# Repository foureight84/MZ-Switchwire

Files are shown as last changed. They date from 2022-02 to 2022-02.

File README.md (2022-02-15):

## Anycubic Mega Zero v1 Switchwire Mod

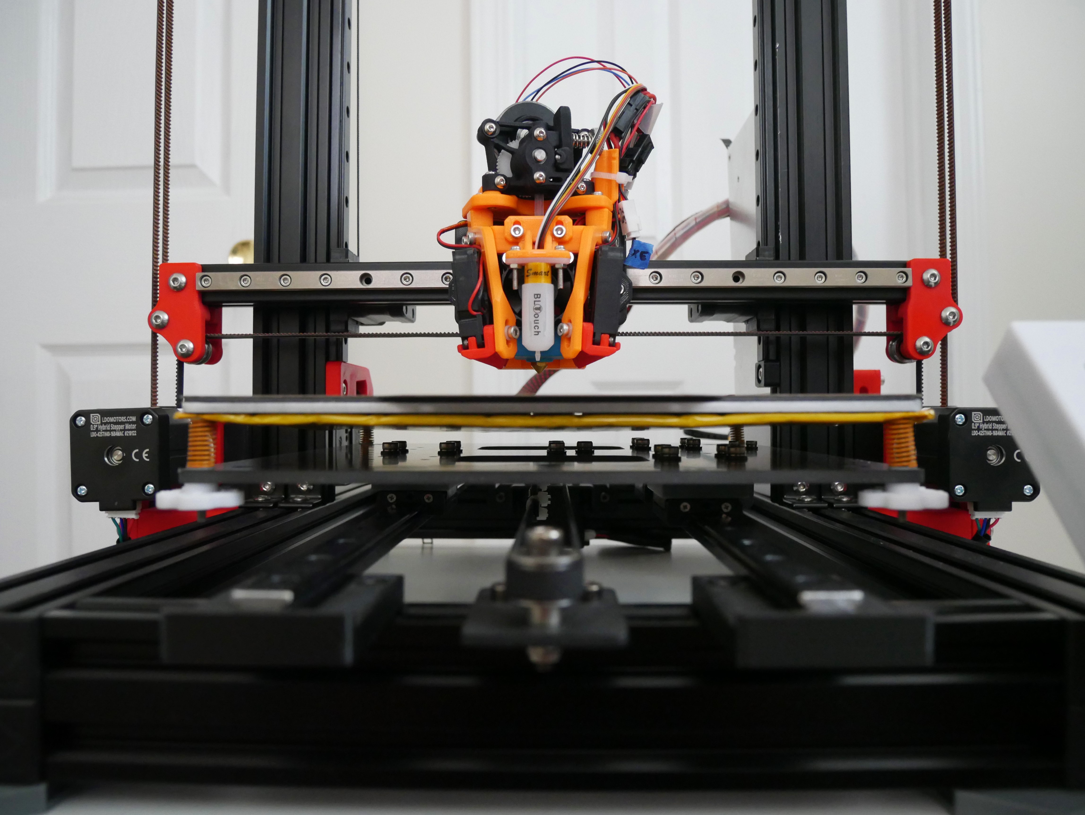
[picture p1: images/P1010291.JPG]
MZ Switchwire


### [390mm X-Axis with MGN9H](https://foureight84.github.io/Anycubic-Mega-Zero-1.0%20-%20Switchwire%20MGN9H%20Gantry-sfa.html "View STEP file") - Click for 3D preview
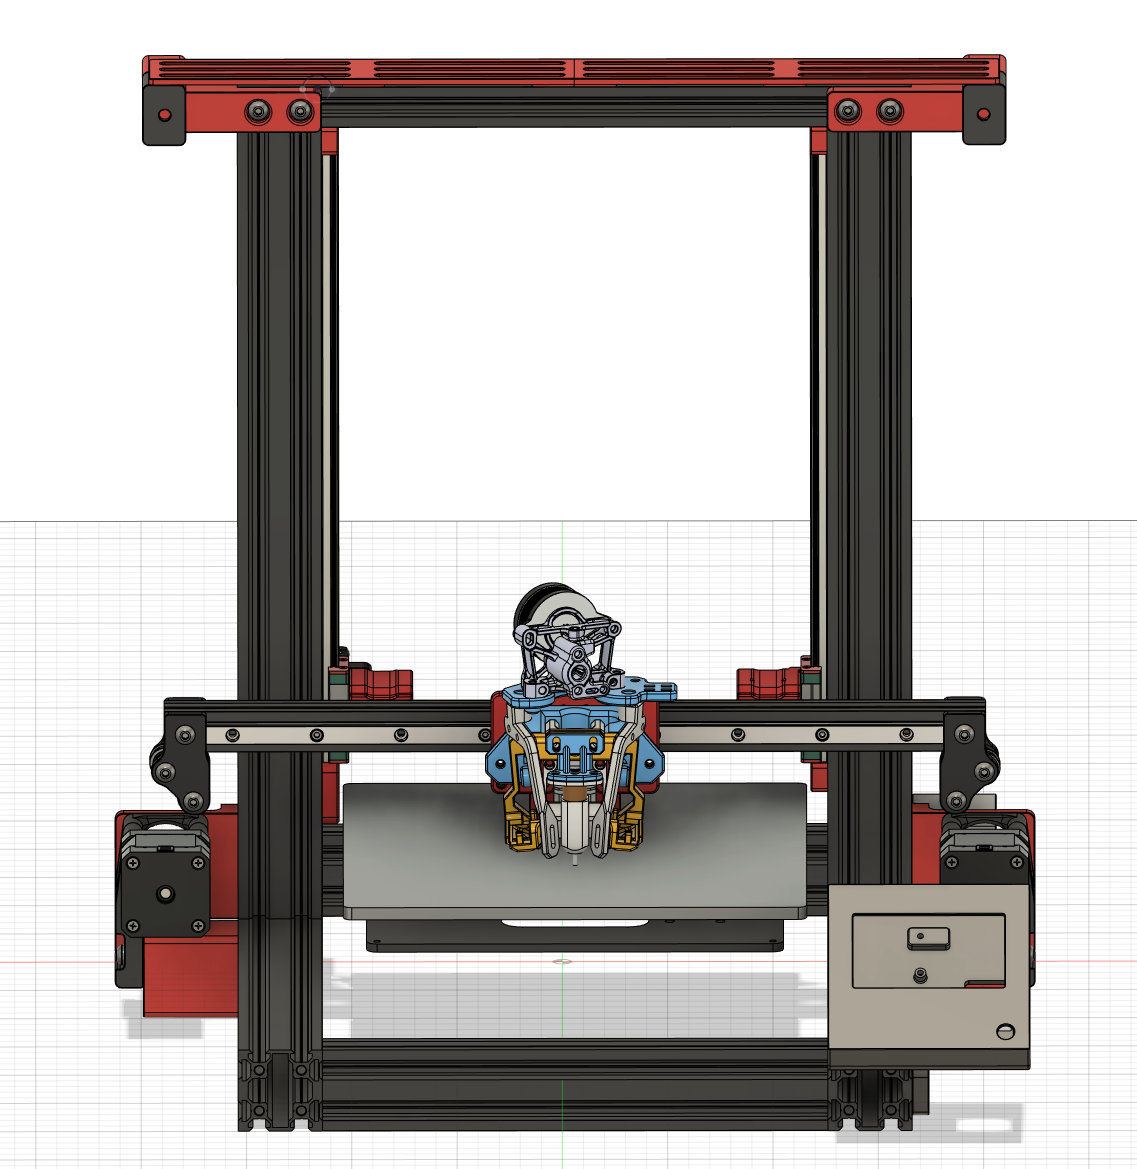
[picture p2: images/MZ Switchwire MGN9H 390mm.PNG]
MZ Switchwire (https://foureight84.github.io/Anycubic-Mega-Zero-1.0%20-%20Switchwire%20MGN9H%20Gantry-sfa.html "View STEP file")


Custom print head assembly plate that is compatible with stock Mega Zero fan shroud or custom Ender 3 solutions like the Manta or HeroMe. Screenshot features the [Manta Cooling](https://www.thingiverse.com/thing:4943125). Swap out MGN9H for MGN12H to use the Voron AfterBurner or StealthBurner.

There is also design for a [custom Y-Carriage design](https://github.com/foureight84/MZ-Switchwire/tree/master/Y-Carriage%20Mod) that can accomodate the original Mega Zero V1 bed, Reprap 220mm heated bed, and Ender 3 235mm heated bed. When using the 235mm Ender 3 heated bed, make sure to use the mirrored Keybak mount and add a Z-stop in its place. 

Parts colored RED are modded parts and adapters to accomodate Switchwire components.

### [340mm X-Axis with MGN12H and AfterBurner](https://foureight84.github.io/Anycubic-Mega-Zero-1.0%20-%20Switchwire%20MGH12H%20Gantry-sfa.html "View STEP file") - Click for 3D preview
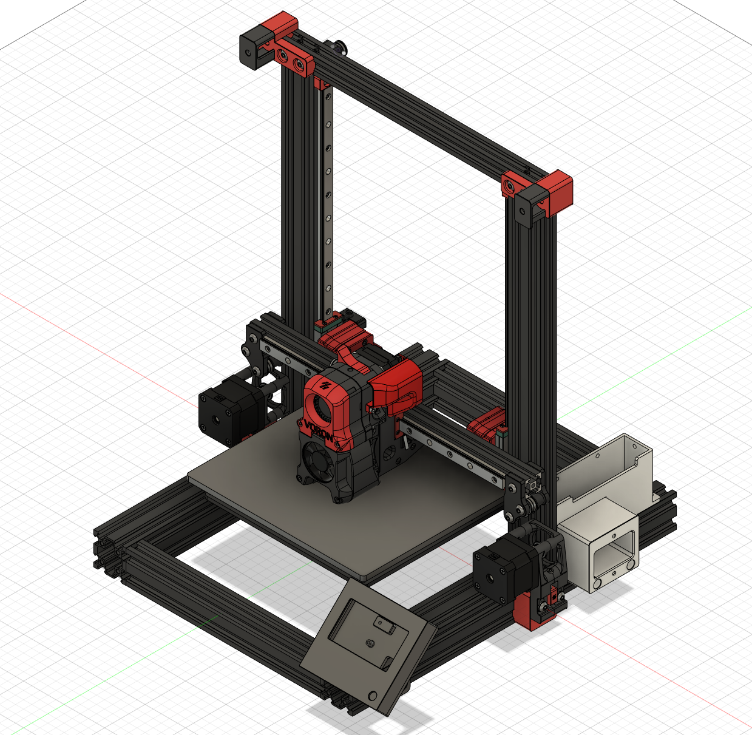
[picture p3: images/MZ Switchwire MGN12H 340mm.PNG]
MZ Switchwire (https://foureight84.github.io/Anycubic-Mega-Zero-1.0%20-%20Switchwire%20MGH12H%20Gantry-sfa.html "View STEP file")


### Mod in action
MZ Switchwire Printing (https://youtu.be/JRjAbpS8Tx0 "MZ Switchwire Printing")

MZ Switchwire Homing (https://youtu.be/6_8q-Ku62cM "MZ Switchwire Homing")

### Print samples
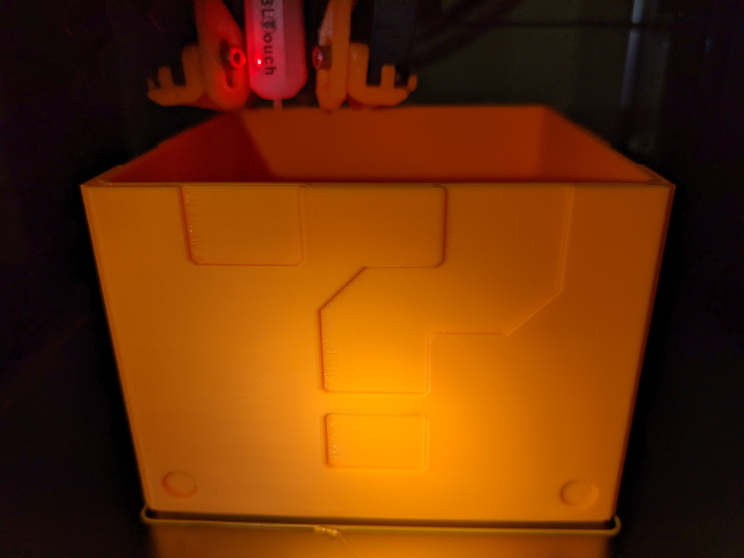
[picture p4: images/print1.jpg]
Print Sample

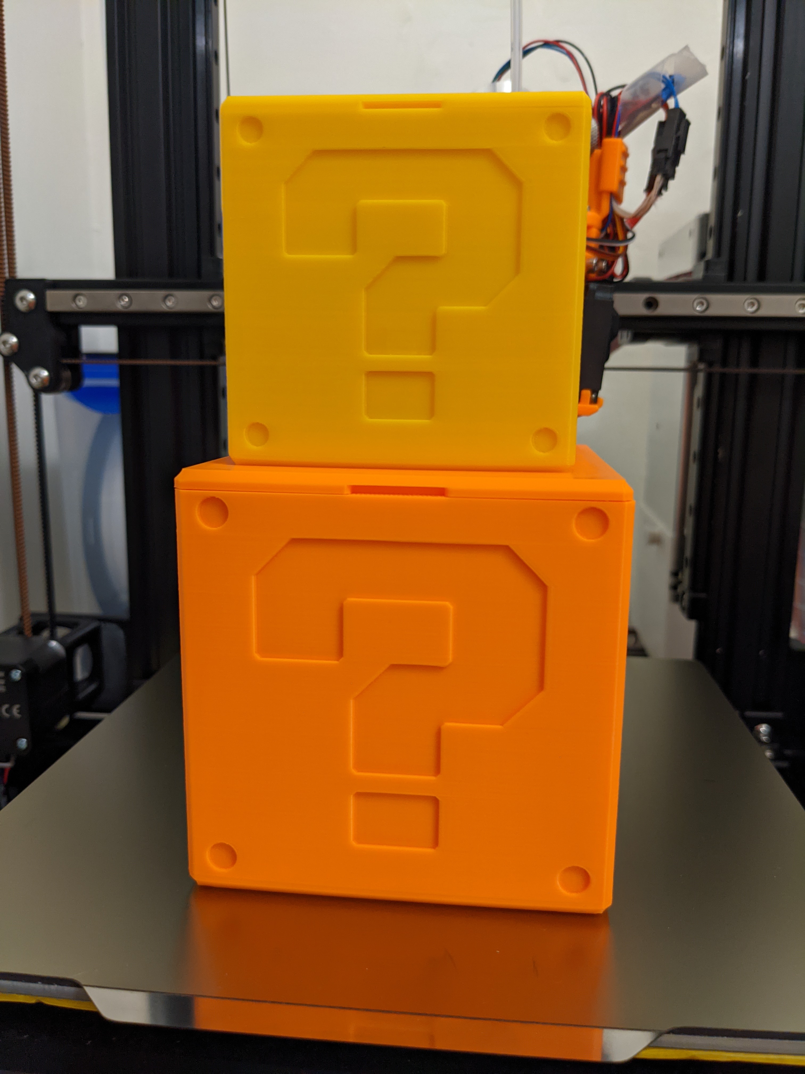
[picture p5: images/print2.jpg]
Print Sample


### Support Link


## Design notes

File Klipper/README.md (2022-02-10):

## Mega Zero Switchwire Klipper config

This configuration utilizes the follwing:
- SKR Mini MZ 1.0 Controller board with TMC2209 drivers
- 220mm BigTreeTech 12v heatbed
- BL Touch
- Custom print head assembly which is a modified and mirrored version of Voron's design. Default Mega Zero X-Axis and Y-Axis homing direction.
- Input shaper enabled. Make sure to run input shaper and pressure advance calibration.
- Stepper motor rotation configuration and current are for 0.9 degree XYZ steppers. (LDO-42STH38-1684MAC)
- Sherpa Mini Direct extruder with Moons (CSE14HRA1L410A-01) 1amp motor.
- Microswiss Hotend

**Make proper adjustments for your steppers**
Stepper current configuration guide: https://docs.vorondesign.com/community/howto/120decibell/calculating_driver_current.html

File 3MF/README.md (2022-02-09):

### Print Instructions

Use the following print settings (default Voron recommendation)

- Layer height: 0.2mm.
- Extrusion width: 0.4mm, forced.
- Infill pecentage: 40%
- Infill type: grid, gyroid, honeycomb, triangle, or cubic.
- Wall count: 4.
- Solid top/bottom layers: 5.
- Supports: NONE.

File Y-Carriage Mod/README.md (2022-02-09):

## Anycubic Mega Zero v1 Custom Y-Carriage

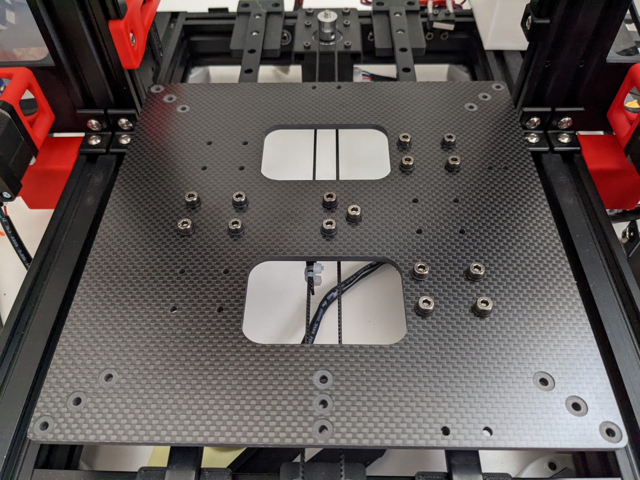
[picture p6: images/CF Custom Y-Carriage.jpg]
CF Y-Carriage


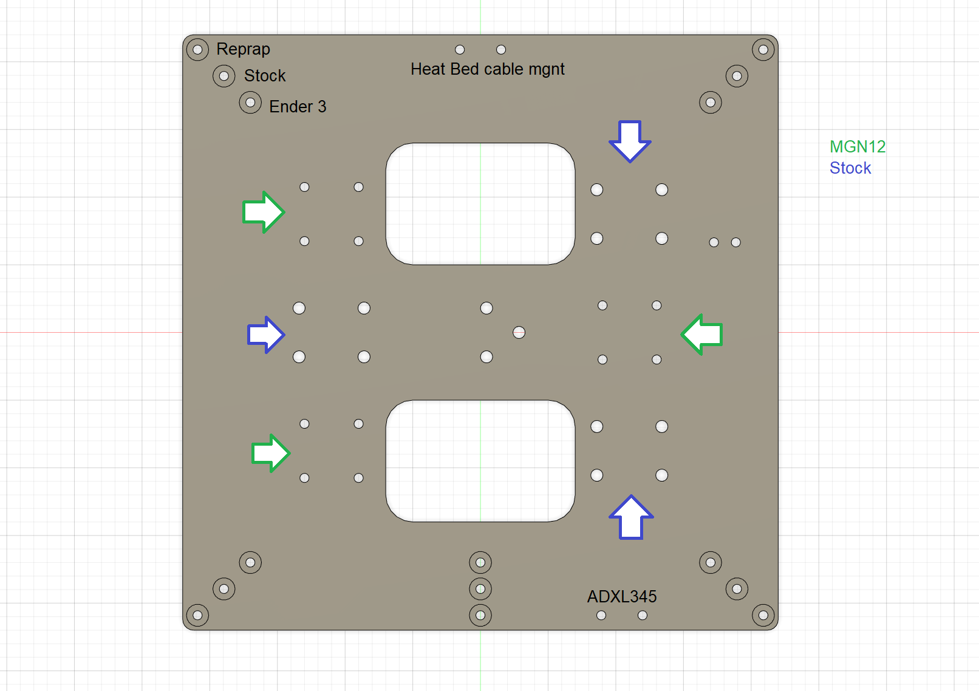
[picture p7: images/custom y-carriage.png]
Custom Y-Carriage Legend


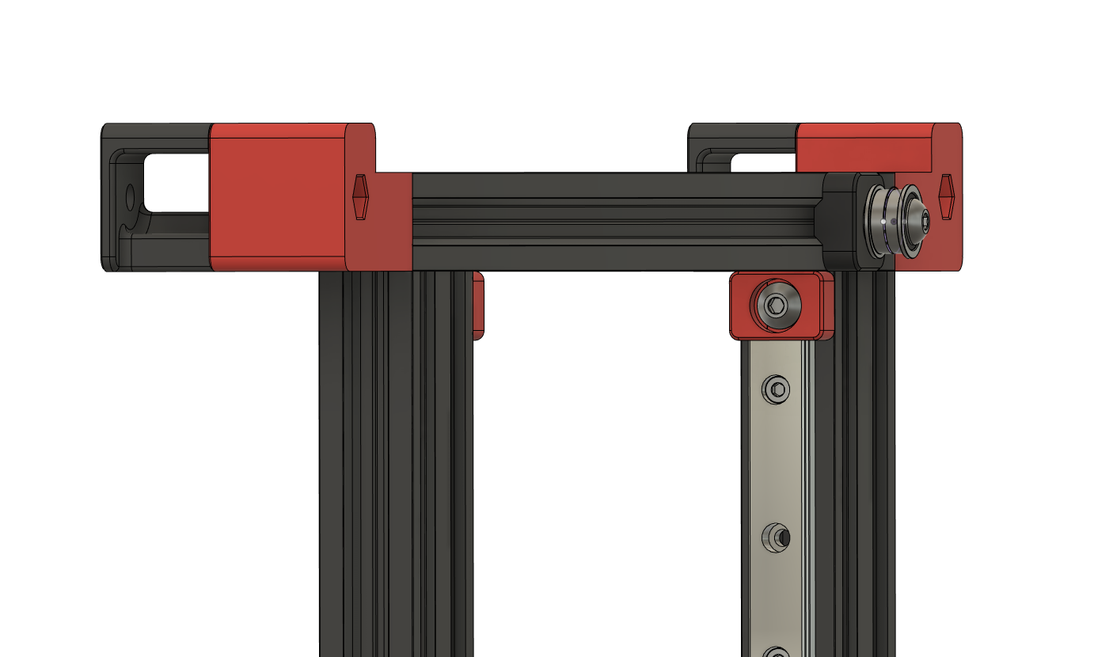
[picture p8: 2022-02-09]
images/Top Idler Back.PNG

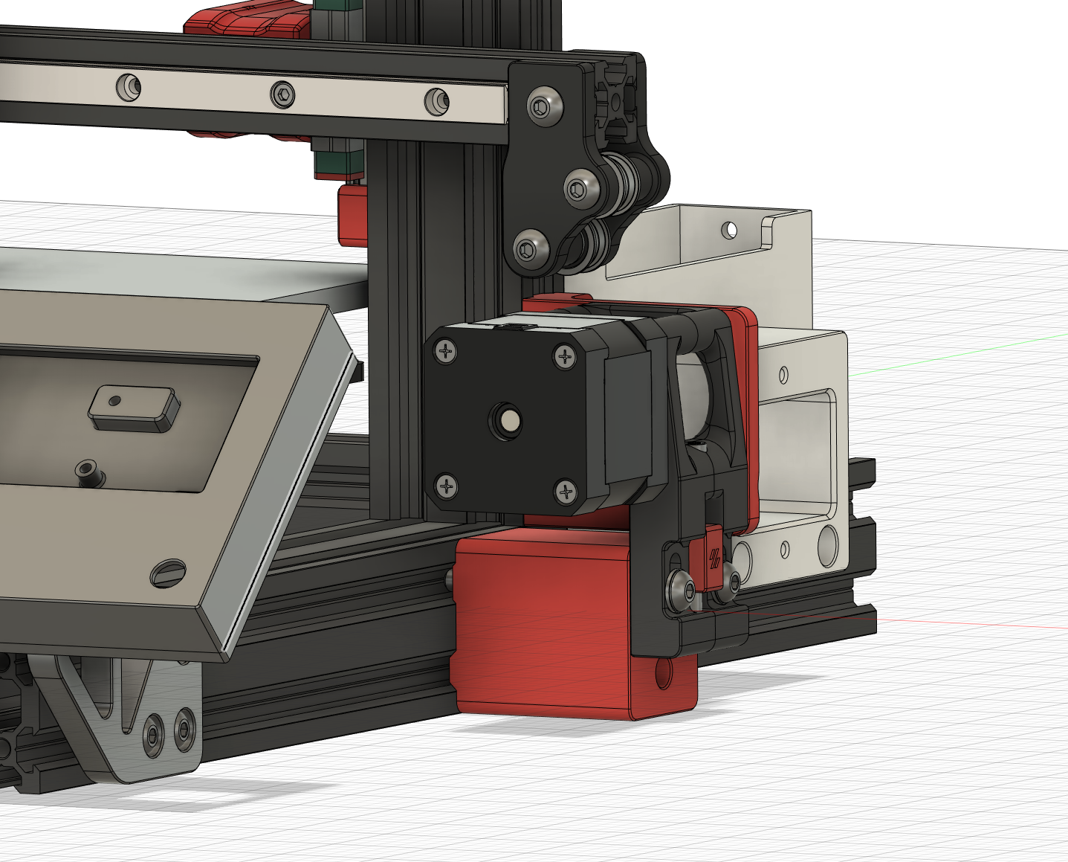
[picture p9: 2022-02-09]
images/Z Motor Mount.PNG

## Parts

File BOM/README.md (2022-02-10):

## BOM

This is a list of parts that corresponds to the mod. These parts are colored RED in the STEP files. You will need to refer to the Voron Switchwire's BOM list and installation manual associated with "OEM" parts (e.g. AfterBurner and clockwork extruder, belt idlers and pulleys, etc).

Links:
VS: https://vorondesign.com/voron_switchwire
VS BOM: https://vorondesign.com/sourcing_guide?model=VS
VS Manual: https://github.com/VoronDesign/Voron-Switchwire/raw/master/Manuals/Assembly_Manual_SW.pdf

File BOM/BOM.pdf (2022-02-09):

# Mega Zero Switchwire Mod BOM

The following list of parts are applicable to modded parts. Refer to Voron Switchwire's BOM list for OEM parts.
** ONLY USE SLIDE IN T-NUTS FOR PARTS CRUCIAL TO KINEMATICS **
390mm Gantry Setup (Use MGN12H for AfterBurner) | 340mm Gantry Setup (Use MGN12H for AfterBurner)
Item | Quantity | Item | Quantity
390mm T-Slot Aluminum Extrusion | 1 | 340mm T-Slot Aluminum Extrusion | 1
350mm MGN9H or MGN12H | 1 | 300mm MGN9H or MGN12H | 1
M3x8mm Socket Head | 12 | M3x8mm Socket Head | 6
M3 Slide-in T-Nuts | 12 | M3 Slide-in T-Nuts | 6
M5x40mm Socket Head | 4 | M5x40mm Socket Head | 4
M5 Slide-in T-Nuts | 4 | M5 Slide-in T-Nuts | 4
M3x30mm Socket Head | 8 | M3x30mm Socket Head | 8

Custom Print Head Mount (Not Required if Using AfterBurner)
M3 Brass Heat Inserts | 12
M3x6mm Socket Head | 2
M3x16mm Socket Head | 4
M3x40mm Socket Head | 3
M2x10mm Selft Tapping Socket Head | 2
KW10 Microswitch | 1
XZ Motor Mounts | | XZ Motor Mounts
M5x60mm Button Head | 4 | M5x35mm Button Head | 4
M5 Washer (.5mm to 1mm thickness) | 4 | M5 Washer (.5mm to 1mm thickness) | 4
M5 Slide-in T-Nuts | 4 | M5 Slide-in T-Nuts | 4
M4x16mm Socket Head | 4 | M4x16mm Socket Head | 4
M4 Slide-in T-Nuts | 2 | M4 Slide-in T-Nuts | 2

XZ Motor Fences
M5x10mm Button Head | 4
M5 Slide-in T-Nuts | 4

XZ Top Idler Wings
M5x10mm Button Head | 4
M5 Slide-in T-Nuts | 4
M5x40mm Button Head | 2
M5 Hex Nut | 2

Z-Axis
300mm MGN12H | 2
M3x8mm Socket Head | 12
M3 Slide-in T-Nuts | 12
M5x10mm | 3
M5 Slide-in T-Nuts | 3

Y-Axis
MGN12H 400m | 2
Additional MGN12H Block | 1
M3x8mm Socket Head | 20
M3 Hex Lock Nut | 8

Keybak Mount and Idler
M5x10mm | 1
M5x20mm | 1
M5 Slide-in T-Nuts | 2
M3 Brass Heat Insert | 2
M3x12mm | 2

LCD Mount
M5x10mm Button Head | 3
M5 Slide-in T-Nuts or rotating T-Nuts | 3
M3x10mm | 2
M2.5 harvest from printer | 4

Power Supply
M4x30mm Socket Head | 2
M4x8mm Socket Head | 4
M4 Slide-in T-Nuts or rotating T-Nuts | 4
M3x8mm | 2

NOT NEEDED

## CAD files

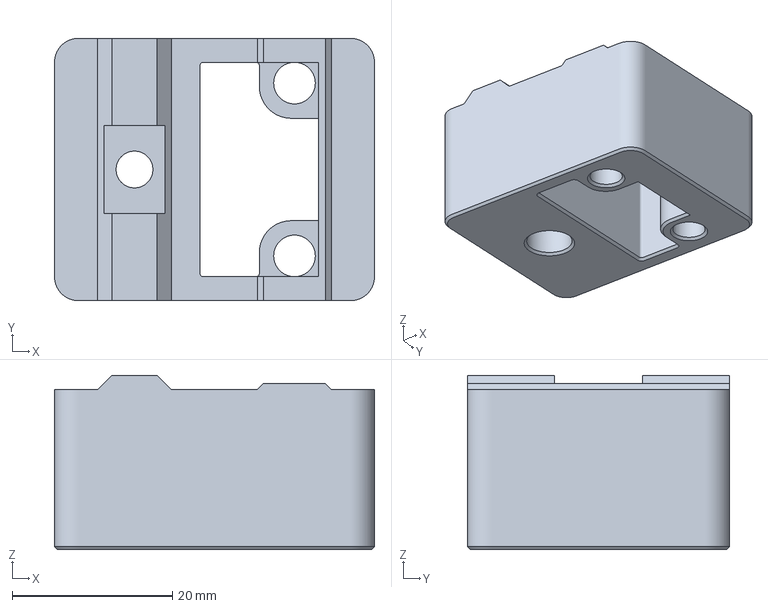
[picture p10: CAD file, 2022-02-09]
3MF/340mm Gantry Setup/XZ Motor - Right.3mf
40.0 x 32.8 x 21.8 mm

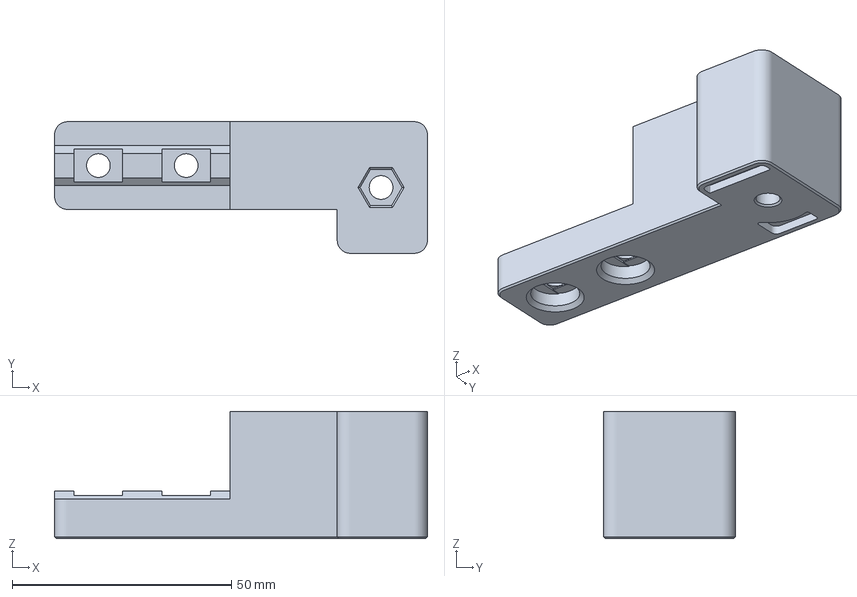
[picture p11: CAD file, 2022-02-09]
3MF/390mm Gantry Setup/XZ Top Bearing - Right.3mf
85.0 x 30.0 x 29.0 mm

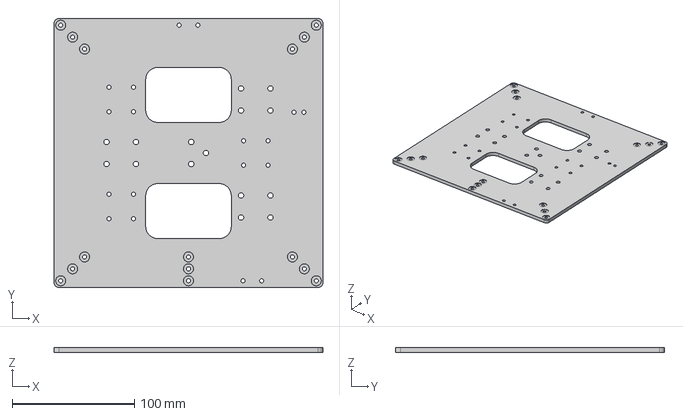
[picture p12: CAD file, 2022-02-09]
Y-Carriage Mod/Y-Carriage v3.step
220.0 x 220.0 x 4.00 mm

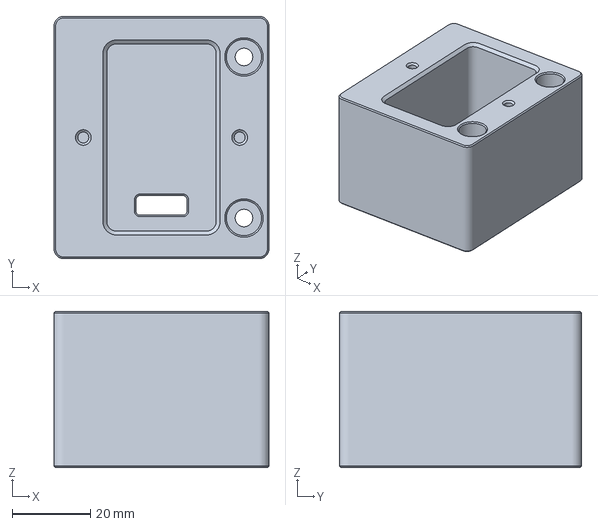
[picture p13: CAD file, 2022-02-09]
3MF/390mm Gantry Setup/Power Supply IEC320 C14 Switch Housing.3mf
55.0 x 62.0 x 40.0 mm

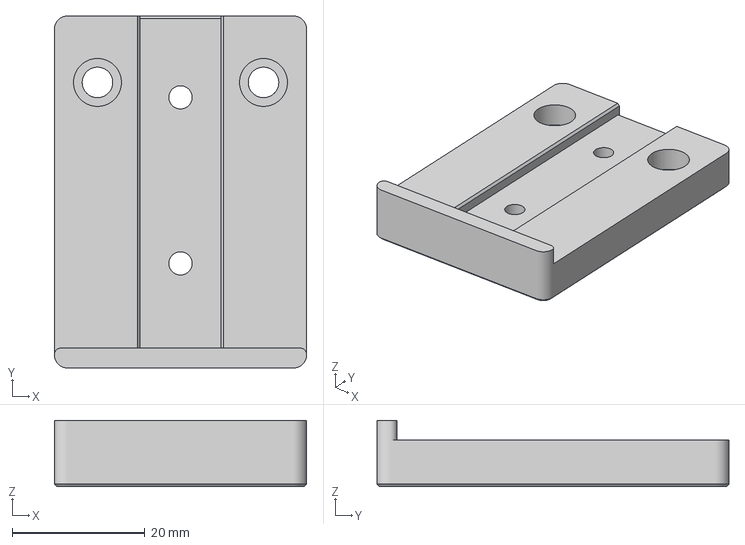
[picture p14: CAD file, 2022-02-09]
Y-Carriage Mod/Y-Axis MGN12 - Front.3mf
38.0 x 53.0 x 10.0 mm

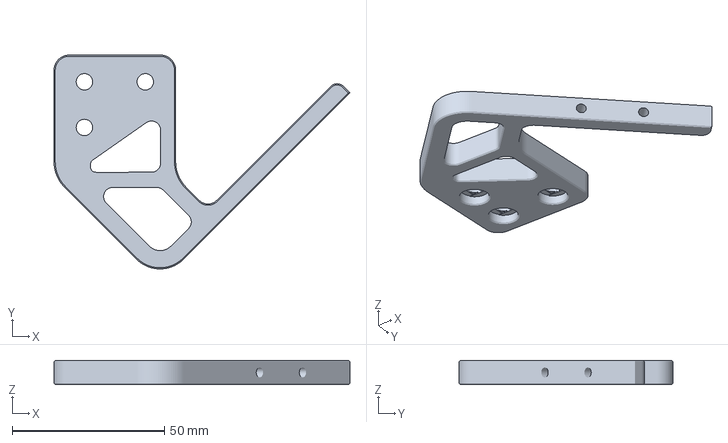
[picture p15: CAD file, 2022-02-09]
3MF/340mm Gantry Setup/LCD Mount Bracket.3mf
97.3 x 70.3 x 8.00 mm

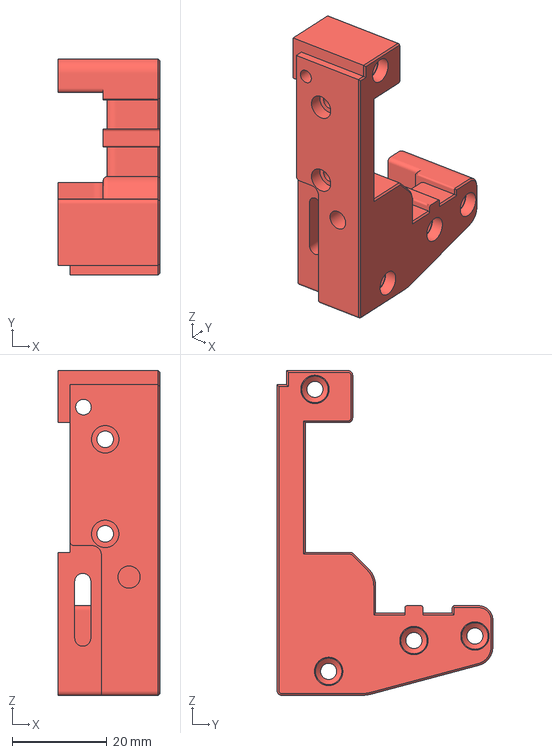
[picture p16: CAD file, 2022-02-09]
3MF/390mm Gantry Setup/X-Carriage MGN12H - Right.3mf
21.6 x 45.6 x 68.8 mm

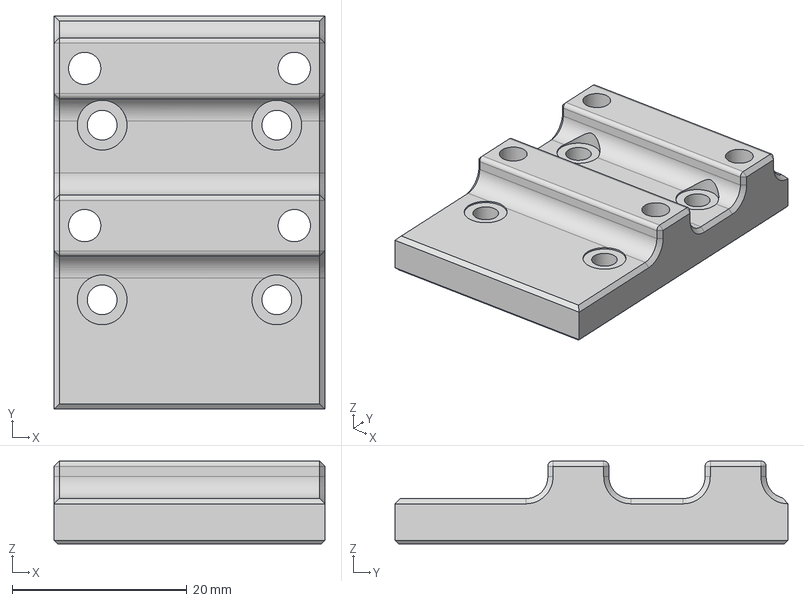
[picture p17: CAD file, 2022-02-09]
Y-Carriage Mod/Y-Axis MGN12 Block Carriage Adapter v2.step
31.0 x 45.0 x 9.50 mm

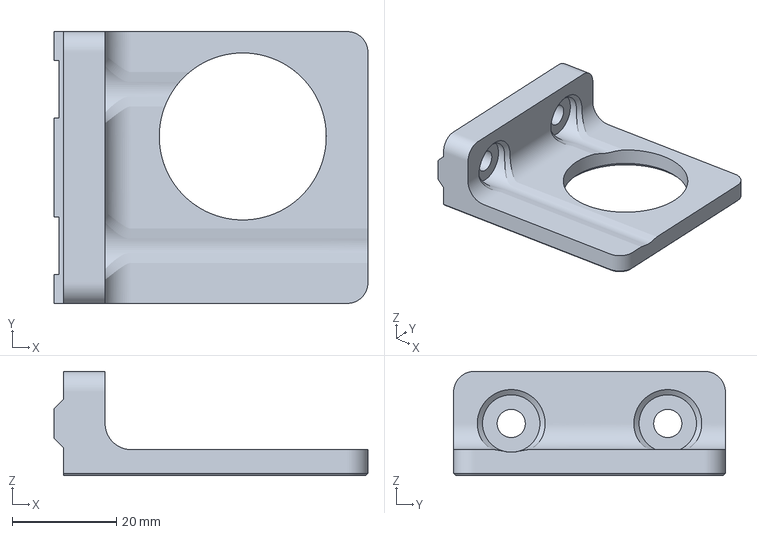
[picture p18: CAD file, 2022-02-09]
3MF/340mm Gantry Setup/Motor Fence - Left.3mf
60.2 x 52.1 x 20.0 mm

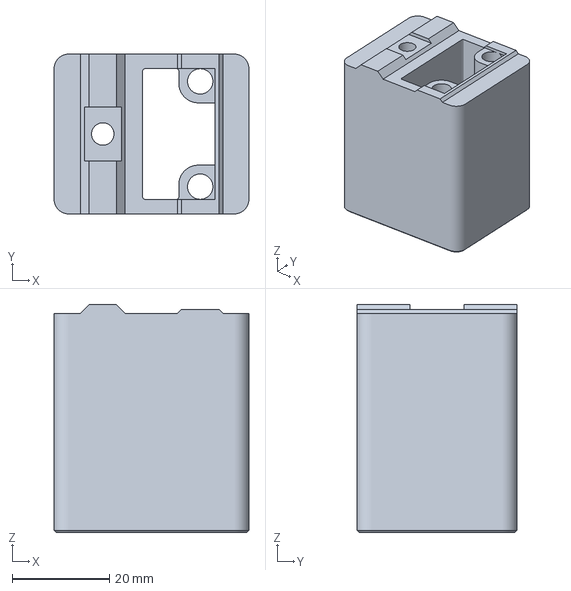
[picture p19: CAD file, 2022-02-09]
3MF/390mm Gantry Setup/XZ Motor - Right.3mf
40.0 x 32.8 x 46.8 mm

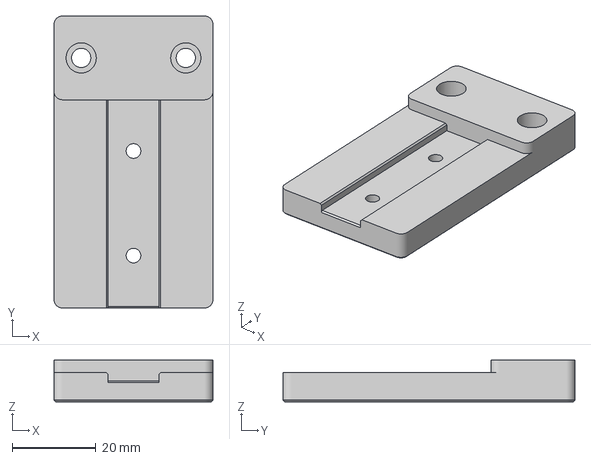
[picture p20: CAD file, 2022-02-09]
Y-Carriage Mod/Y-Axis MGN12 - Back.3mf
38.0 x 69.8 x 10.0 mm

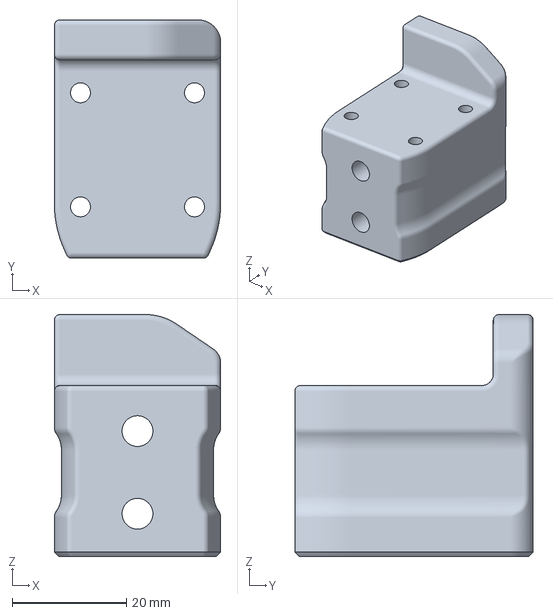
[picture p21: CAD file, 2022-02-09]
3MF/340mm Gantry Setup/Z Bearing Block - Right.3mf
29.2 x 41.8 x 42.4 mm

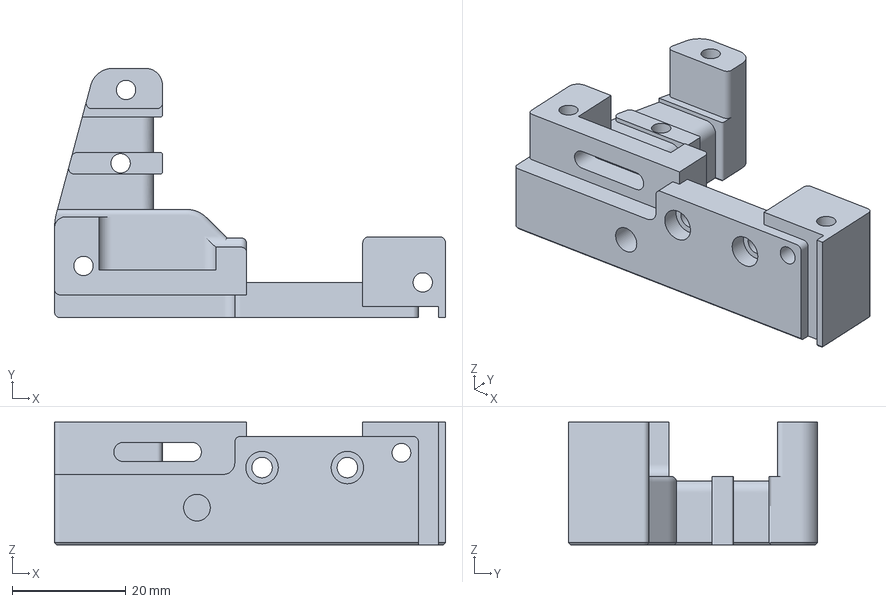
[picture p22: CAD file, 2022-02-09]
3MF/390mm Gantry Setup/X-Carriage MGN9H - Right.3mf
68.8 x 43.8 x 21.6 mm

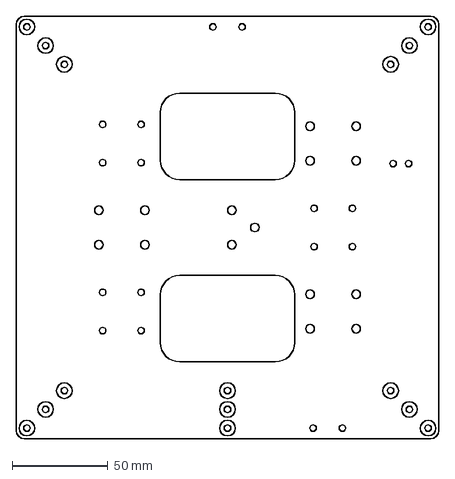
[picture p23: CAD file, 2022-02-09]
Y-Carriage Mod/y-carriage_v3_clean.dxf
220.0 x 220.0 mm

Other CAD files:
3MF/340mm Gantry Setup/XZ Motor - Left.3mf
3MF/340mm Gantry Setup/X-Carriage MGN9H - Left.3mf
3MF/390mm Gantry Setup/XZ Motor - Left.3mf
3MF/340mm Gantry Setup/Hotend Plate - Ender 3 MZv1 Compat.3mf
3MF/340mm Gantry Setup/Hotend Plate Spacer.3mf
3MF/340mm Gantry Setup/Keybak Mount - Inner Shell.3mf
3MF/340mm Gantry Setup/Keybak Mount - Outter Shell.3mf
3MF/340mm Gantry Setup/LCD Housing Bottom.3mf
3MF/340mm Gantry Setup/LCD Housing Top.3mf
3MF/340mm Gantry Setup/LRS 350 12v24v Housing.3mf
3MF/340mm Gantry Setup/Motor Fence - Right.3mf
3MF/340mm Gantry Setup/X-Carriage MGN12H - Left.3mf
3MF/340mm Gantry Setup/XZ Top Idler - Left.3mf
3MF/340mm Gantry Setup/XZ Top Idler - Right.3mf
3MF/340mm Gantry Setup/Z Bearing Block - Left.3mf
3MF/340mm Gantry Setup/Z Stop.3mf
3MF/390mm Gantry Setup/Hotend Plate - Ender 3 MZv1 Compat.3mf
3MF/390mm Gantry Setup/Hotend Plate Spacer.3mf
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

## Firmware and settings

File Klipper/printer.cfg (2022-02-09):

# This file contains common pin mappings for the BIGTREETECH SKR mini
# MZ v1.0. To use this config, the firmware should be compiled for the
# STM32F103 with a "28KiB bootloader" and USB communication. Also,
# select "Enable extra low-level configuration options" and configure
# "GPIO pins to set at micro-controller startup" to "!PA14".

# The "make flash" command does not work on the SKR mini MZ. Instead,
# after running "make", copy the generated "out/klipper.bin" file to a
# file named "firmware.bin" on an SD card and then restart the SKR
# mini MZ with that SD card.

# See docs/Config_Reference.md for a description of parameters.

# Note: This board has a design flaw in its thermistor circuits that
# cause inaccurate temperatures (most noticeable at low temperatures).

# PETG CONFIG #

[stepper_x]
step_pin: PB13
dir_pin: !PB12
enable_pin: !PB14
microsteps: 16
rotation_distance: 40
endstop_pin: PC0
position_endstop: -40
position_min: -40
position_max: 220
homing_speed: 100
full_steps_per_rotation: 400

[tmc2209 stepper_x]
uart_pin: PC11
tx_pin: PC10
uart_address: 0
run_current: 1.1
#hold_current: 0.7
stealthchop_threshold: 999999

[stepper_y]
step_pin: PB10
dir_pin: PB2
enable_pin: !PB11
microsteps: 16
rotation_distance: 40
endstop_pin: ^PC1
position_endstop: -24
position_min: -24
position_max: 250
homing_speed: 100
full_steps_per_rotation: 400

[tmc2209 stepper_y]
uart_pin: PC11
tx_pin: PC10
uart_address: 1
run_current: 1.1
#hold_current: 0.7
stealthchop_threshold: 999999

[stepper_z]
step_pin: PB0
dir_pin: !PC5
enable_pin: !PB1
microsteps: 16
rotation_distance: 40
endstop_pin: probe:z_virtual_endstop
# position_endstop: 0
position_max: 250
position_min: -2.0
homing_speed: 100
full_steps_per_rotation: 400

[tmc2209 stepper_z]
uart_pin: PC11
tx_pin: PC10
uart_address: 2
run_current: 1.1
#hold_current: 0.7
stealthchop_threshold: 999999

# Sherpa Mini
[extruder]
step_pin: PB3
dir_pin: !PB4
enable_pin: !PD2
microsteps: 16
rotation_distance: 22.67895
gear_ratio: 50:10
full_steps_per_rotation: 200 #1.8deg Motor
nozzle_diameter: 0.400
filament_diameter: 1.750
heater_pin: PC8
sensor_type: NTC 100K beta 3950
sensor_pin: PA0
min_temp: 0
max_temp: 285
pressure_advance: 0.1659
max_extrude_only_distance: 1400.0
max_extrude_only_velocity: 75.0
max_extrude_only_accel: 1500
#control: pid

[tmc2209 extruder]
uart_pin: PC11
tx_pin: PC10
uart_address: 3
run_current: 0.7
#hold_current: 0.19
#interpolate: True
stealthchop_threshold: 999999

[heater_bed]
heater_pin: PC9
sensor_type: EPCOS 100K B57560G104F
sensor_pin: PC3
min_temp: 0
max_temp: 130

[heater_fan nozzle_cooling_fan]
pin: PC7

[fan]
pin: PC6


[mcu]
serial: /dev/serial/by-id/usb-Klipper_stm32f103xe_30FFD9054255353830721857-if00

[mcu rpi]
serial: /tmp/klipper_host_mcu

[adxl345]
cs_pin: rpi:None

[resonance_tester]
accel_chip: adxl345
probe_points:
    100,100,20  # an example

[input_shaper]
shaper_freq_x: 55.2
shaper_type_x: mzv
shaper_freq_y: 46.6
shaper_type_y: mzv

[printer]
kinematics: corexz
max_velocity: 300
max_accel: 3000
max_accel_to_decel: 1500
max_z_velocity: 100
max_z_accel: 1000
square_corner_velocity: 4.0
#max_accel: 10000 #input shaper
#max_accel_to_decel: 10000 #input shaper

[static_digital_output usb_pullup_enable]
pins: !PA14

[bltouch]
sensor_pin: ^PC14
control_pin: PA1
x_offset: 0.027
y_offset: -40
#z_offset: 0.515
pin_move_time: 0.680
stow_on_each_sample: True
probe_with_touch_mode: True
#pin_up_reports_not_triggered: True
#pin_up_touch_mode_reports_triggered: False

[display]
lcd_type: st7920
cs_pin: EXP1_7
sclk_pin: EXP1_6
sid_pin: EXP1_8
encoder_pins: ^EXP1_5, ^EXP1_3
click_pin: ^!EXP1_2

[output_pin beeper]
pin: EXP1_1

[safe_z_home]
home_xy_position: 110,150
speed: 100.0
z_hop: 10
z_hop_speed: 10.0
move_to_previous: False

[bed_mesh]
speed: 120
horizontal_move_z: 5
mesh_min: 5,5
mesh_max: 210,210
probe_count: 5,5
fade_start: 1.0
mesh_pps: 2,2

[gcode_macro G29]
gcode:
    BED_MESH_CALIBRATE


[bed_screws]
speed: 120
screw1: 11,11
screw2: 209,209
screw3: 209,11
screw4: 11,209


[board_pins]
aliases:
    # EXP1 header
    EXP1_1=PB5, EXP1_3=PA9,   EXP1_5=PA10, EXP1_7=PB8, EXP1_9=<GND>,
    EXP1_2=PA15, EXP1_4=<RST>, EXP1_6=PB9,  EXP1_8=PB15, EXP1_10=<5V>

# See the sample-lcd.cfg file for definitions of common LCD displays.

#MainSail Config
[virtual_sdcard]
path: ~/gcode_files

[display_status]

[pause_resume]

[menu __main __octoprint]
type: disabled

#[gcode_macro PAUSE]
#rename_existing: BASE_PAUSE
#default_parameter_X: 230    #edit to your park position
#default_parameter_Y: 230    #edit to your park position
#default_parameter_Z: 10     #edit to your park position
#default_parameter_E: 1      #edit to your retract length
#gcode:
#    SAVE_GCODE_STATE NAME=PAUSE_state
#    BASE_PAUSE
#    G91
#    G1 E-{E} F2100
#    G1 Z{Z}
#    G90
#    G1 X{X} Y{Y} F6000

#[gcode_macro RESUME]
#rename_existing: BASE_RESUME
#default_parameter_E: 1      #edit to your retract length
#gcode:
#    G91
#    G1 E{E} F2100
#    G90
#    RESTORE_GCODE_STATE NAME=PAUSE_state MOVE=1
#    BASE_RESUME

[gcode_macro CANCEL_PRINT]
rename_existing: BASE_CANCEL_PRINT
gcode:
    G91 ;relative positioning
	G1 E-1 F300 ;retract the filament a bit before lifting the nozzle, to release some of the pressure
	G1 Z+25.0 E-5 ;X-20 Y-20 F{speed_travel} ;move Z up a bit and retract filament even more
	G28 X0 ;move X to min endstops, so the head is out of the way
	G90 ;Absolute positioning
	G1 Y200 F3000 ;Present print
    TURN_OFF_HEATERS
    CLEAR_PAUSE
    SDCARD_RESET_FILE
    BASE_CANCEL_PRINT
    M84 ;steppers off
    M117 Cancelled ...

[temperature_sensor raspberry_pi]
sensor_type: temperature_host
min_temp: 10
max_temp: 100

[temperature_sensor mcu_temp]
sensor_type: temperature_mcu
min_temp: 0
max_temp: 100


[gcode_macro PRESENT_PRINT]
gcode:
    M107 ; Fan off
    G91 ;relative positioning
    G1 E-1 F300 ;retract the filament a bit before lifting the nozzle, to release some of the pressure
    G1 Z+25.0 E-5 ;X-20 Y-20 F{speed_travel} ;move Z up a bit and retract filament even more
    G28 X0 ;move X to min endstops, so the head is out of the way
    G90 ;Absolute positioning
    G1 Y200 F3000 ;Present print


[gcode_macro GANTRY_LEVEL]
gcode:
    G21 ;metric values
	G90 ;absolute positioning
	M117 Homing X/Y/Z ...
	G28 ; move X/Y/Z to min endstops
	M400
	M117 Leveling X Gantry ...
	G1 F200 X120 Z220
	M400 
	G1 F200 X120 Z150
	M400 
	M117 Re-Homing X/Y/Z ...
	G28 ; move X/Y/Z to min endstops
	M117 Finished ...


[gcode_macro Load_PLA]
gcode:
    G28 ; Home Axis
    G21 ;Let the printer know you are following this point with metric values
    G90 ;Let the printer know you are using absolute positioning
    M117 Load Filament Now ;Display message on LCD-display 
    M109 S210.00 ;Heat hotend to 210C for PLA
    G28 X Y ;move extruder back to front left corner
    G1 Z15.0 ;move the platform down 15mm
    M400 ;Wait for Temp
    G92 E0 ;Reset the position of the extruder
    G1 E220 F400 ;Feed 220 mm of filament at 400 mm minute speed change 220 to 100mm longer than the lenght of your bowdentube 
    M400 ;Wait for feed
    G92 E0 ;Reset the position of the extruder
    M117 Filament Loaded ... ;Display message on LCD-display 


[gcode_macro Load_PETG]
gcode:
    G28 ; Home Axis
    G21 ;Let the printer know you are following this point with metric values
    G90 ;Let the printer know you are using absolute positioning
    M117 Load Filament Now ;Display message on LCD-display 
    M109 S235.00 ;Heat hotend to 235C for PETG
    G28 X Y ;move extruder back to front left corner
    G1 Z15.0 ;move the platform down 15mm
    M400 ;Wait for Temp
    G92 E0 ;Reset the position of the extruder
    G1 E220 F400 ;Feed 220 mm of filament at 400 mm minute speed change 220 to 200mm longer than the lenght of your bowdentube
    M400 ;Wait for feed
    G92 E0 ;Reset the position of the extruder
    M117 Filament Loaded ... ;Display message on LCD-display 


[gcode_macro Unload_PLA]
gcode:
    G28 ; Home Axis
    G21 ;Let the printer know you are following this point with metric values
    G90 ;Let the printer know you are using absolute positioning
    M117 Heating Ext ... ;Display message on LCD-display 
    M109 S210.00 ;Heat hotend to 210C for PLA 
    G28 X Y ;move extruder back to front left corner
    G1 Z15.0 ;move the platform down 15mm
    M400 ;Wait for Temp
    G92 E0 ;Reset the position of the extruder
    G1 E10 F100 ; Extrude a short distance before unloading to avoid blob forming
    G92 E0 ;Reset the position of the extruder
    G1 E-130 F100 ;Retract 130 mm of filament at 2000 mm minute speed change 130 to the lenght of your bowdentube
    M400 ;Wait for Filament to eject
    G92 E0 ;Reset the position of the extruder
    M117 REMOVE FILAMENT NOW ;Display message on LCD-display to remove the filament
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

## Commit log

2022-02-09 Added project files
    [Hotend Plate - Ender 3 MZv1 Compat.3mf, Hotend Plate Spacer.3mf, Keybak Mount - Inner Shell.3mf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]
2022-02-09 added y-carriage files
    [Y-Axis MGN12 - Back.3mf, Y-Axis MGN12 - Front.3mf, Y-Axis MGN12 Block Carriage Adapter v2.3mf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]
2022-02-09 added print sample images
2022-02-09 updated y-carriage readme
2022-02-09 added BOM
    [BOM.xlsx, XZ Motor - Left.3mf, XZ Motor - Right.3mf]
2022-02-09 updated bom and step files
    [BOM.xlsx]
2022-02-09 Updated STEP files, BOM, and added README for Klipper configuration
    [BOM.xlsx]
2022-02-09 added print settings
2022-02-09 updated bom
    [BOM.xlsx]
2022-02-10 added BOM README. updated step files and preview
